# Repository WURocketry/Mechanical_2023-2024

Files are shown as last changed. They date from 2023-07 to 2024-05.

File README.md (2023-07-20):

# Mechanical
Mechanical Design Repository

* CAD Models

### Subteam Folders
Subteams are free to modify their own folder as they like - keep all your subteam related files/articles/figures within that folder.

### Subteam Branches
The "main" Mechanical repository is organized into 5 subteam development branches:

* "dev/aero"
* "dev/avionics"
* "dev/payload"
* "dev/r&p"
* "dev/structures"

Subteam changes should be pushed and pull requests made only to the respective development subteam branch!

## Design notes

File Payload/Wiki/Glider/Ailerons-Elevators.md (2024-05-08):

### How do planes turn with their ailerons?
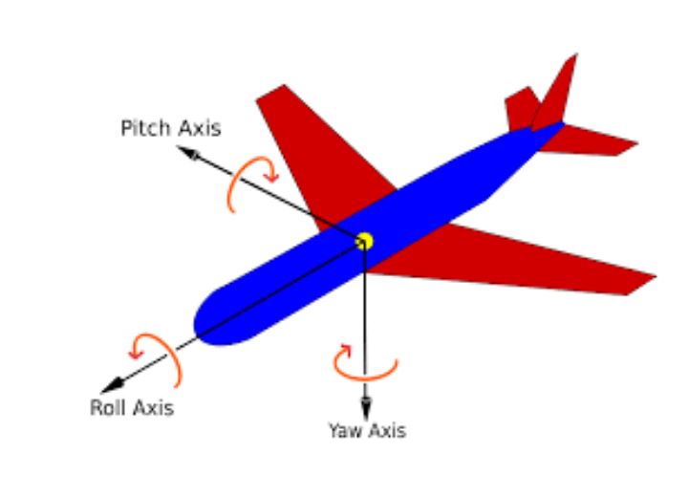
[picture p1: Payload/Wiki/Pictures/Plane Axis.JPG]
Plane Axis


An aircraft is turned by banking the wing. This is achieved via aileron deflection (the flaps on the wings). For example, if wanting to turn left, the left aileron would go up and the right aileron would go down. The right wing would generate comparatively more lift and cause the aircraft to rotate along the roll axis toward the left wing. Breaking down the lift into its constituent vectors, it can be seen the aircraft will turn left. However, in generating lift by deflecting the airflow, more drag is necessarily incurred on the right wing. This causes the aircraft to rotate along the yaw axis toward the right wing. This is known as adverse yaw. A rudder can be used to counteract this skidding effect by turning it opposite the direction of the slip. 

Aside: To compensate for the decrease in lift due to ailerons, consider the use of an elevator to maintain altitude

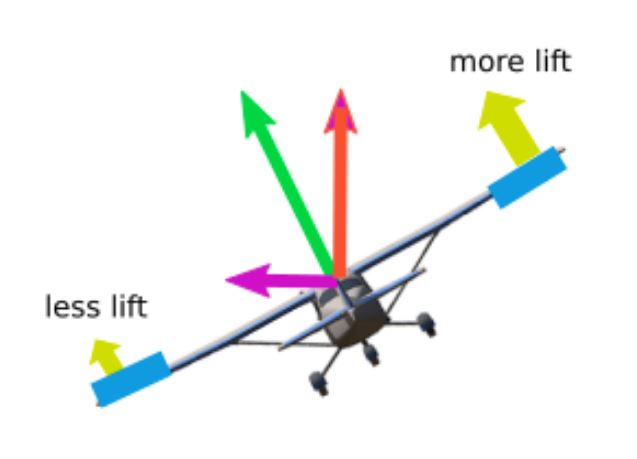
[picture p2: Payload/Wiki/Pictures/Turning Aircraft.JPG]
Turning Aircraft


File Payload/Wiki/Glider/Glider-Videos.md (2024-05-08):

## These are all videos that I've watched when trying to learn about gliders and planes

[Can a plane fly with offset wings?](https://youtu.be/_6qv-7W1oXM?si=U3Id_NZv6tD9XoEl)

[Air powered plane](https://youtu.be/Ho2l1K4Jprg?si=fbuXTHSk7X7ttCQ5)

[In-air deployed Wings](https://youtu.be/bcsHTJZXA5M?si=50AS-EBUmxvygqyN)

[Building RC Planes with a 3D printer](https://youtu.be/Fi35p8bJMsA?si=6PIT_olx3aTciqMt)

[Lifting body Aircraft](https://youtu.be/PmRX-CzJbd0?si=Z4fhiQjwDQRD28tA)

[Shuttle Drop Glider](https://youtu.be/U6PQD6Xdg0g?si=6WSX85FjxjvWDiC7)

[Solid Wood Glider](https://youtu.be/7oy3jXu_DmY?si=__zFUrIsEFcsmnhw)

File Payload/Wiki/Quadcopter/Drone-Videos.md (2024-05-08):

## These are all videos that I've watched when trying to learn about drones and quadcopters

[Building the world's fastest drone](https://youtu.be/szxRORFl_lc?si=UBYPmssPb1zO7FjE)

[Ground Effect Quadcopter](https://youtu.be/66PmaluCvbU?si=f91-r_Z-RgY1vGZZ)

[Vertical Drone with Flaps](https://youtu.be/AnGWM0yDfpo?si=fNXaneckABWPh2j7)

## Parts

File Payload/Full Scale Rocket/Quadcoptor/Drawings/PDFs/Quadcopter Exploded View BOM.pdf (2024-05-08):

ITEM NO. | PART NUMBER | DESCRIPTION | QTY.
1 | Vertical Beam | | 1
2 | Arm Hub | | 1
3 | ECO II Series 2207 | | 4
4 | Left Hinge | | 4
5 | Right Hinge | | 4
6 | Arm | | 4
7 | DAL Fold 2 | | 4
8 | Turnigy 6S 5000 mAh Battery | | 1
9 | Speedy Bee F405 V3 Stacked FC & ESC | | 1
10 | Nosecone | | 1
11 | 1556A24 | Zinc-Plated Steel Corner Bracket | 8
12 | 91772A092 | Passivated 18-8 Stainless Steel Pan Head Phillips Screw | 12
13 | Life Support Electronics Board | | 1
14 | Detachment Eye Nut | | 1
15 | Arm Cushion | | 4
16 | STEMnaut Housing | | 1
17 | Arm Locker | | 4
18 | Hinge Cushion | | 4
19 | 91773A151 | Stainless Steel Decorative Round Head Phillips Screws | 6
20 | 90272A161 | Zinc-Plated Steel Pan Head Phillips Screw | 2
21 | STEMnaut Housing Cap | | 1
22 | 91292A134 | 18-8 Stainless Steel Socket Head Screw | 4
23 | Leadscrew Motor | | 1
24 | Motor Shaft Coupler | | 1
25 | Leadscrew | | 1
SOLIDWORKS Educational Product. For Instructional Use Only.

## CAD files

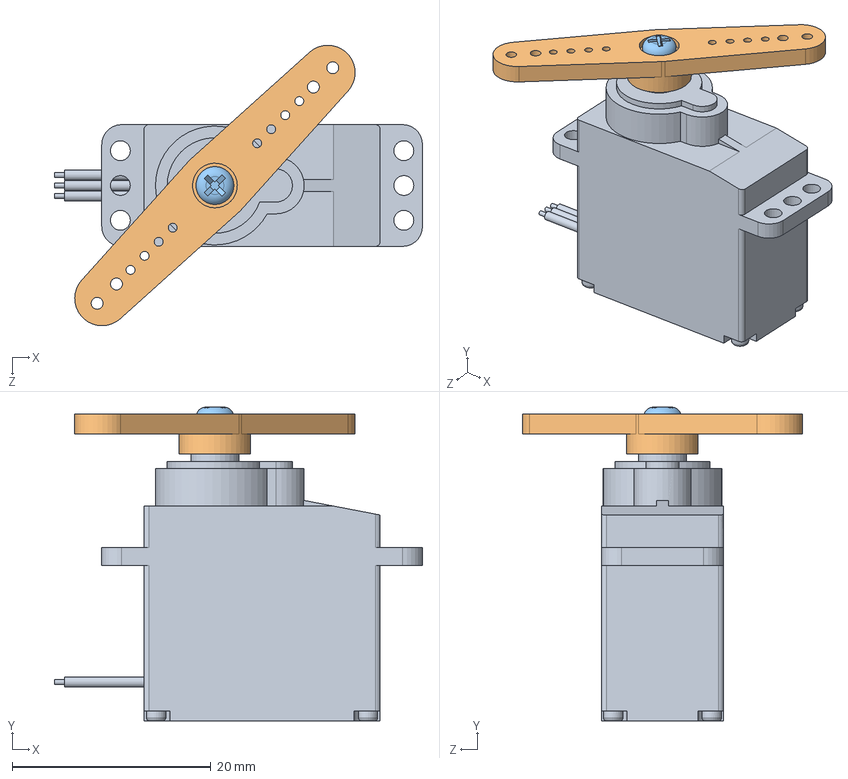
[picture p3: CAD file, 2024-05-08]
Payload/Full Scale Rocket/Quadcoptor/arduino-micro-servo-1.snapshot.13/SM-S2309S.SLDASM
37.0 x 31.5 x 28.2 mm
SM-S2309S
SM-S2309S-Arm
SM-S2309S-Screw

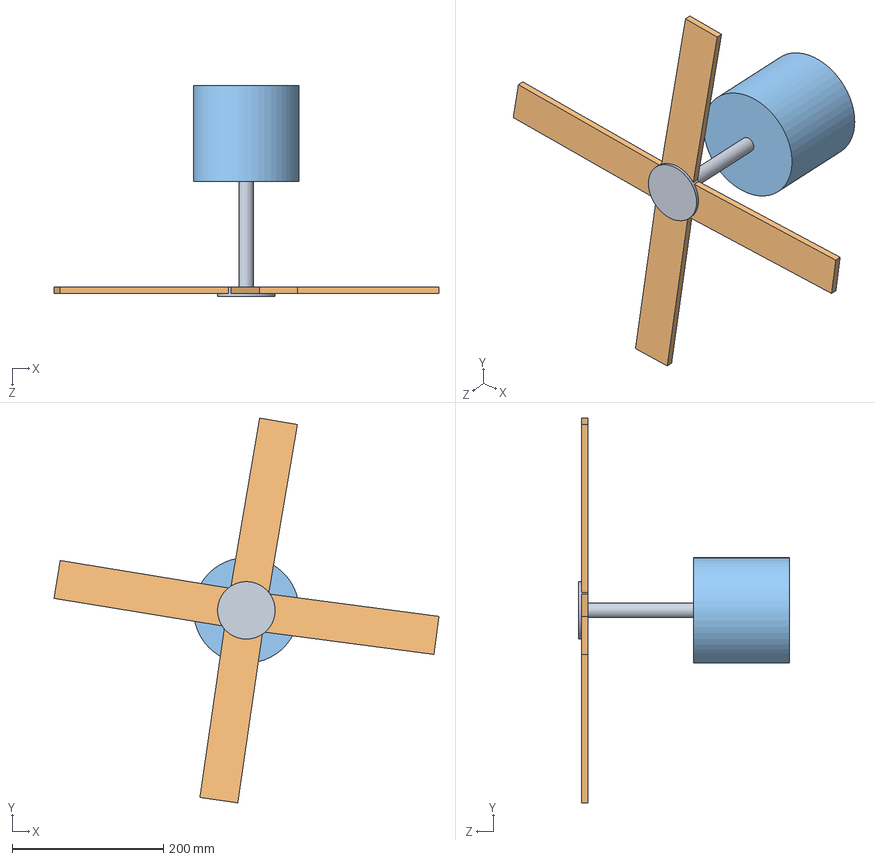
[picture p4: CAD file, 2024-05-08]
Payload/Autorotation Prelim/Autorotation_ASS.SLDASM
509.9 x 509.7 x 279.4 mm
Rotor Shaft
Rotor Blades x 4
Capsule

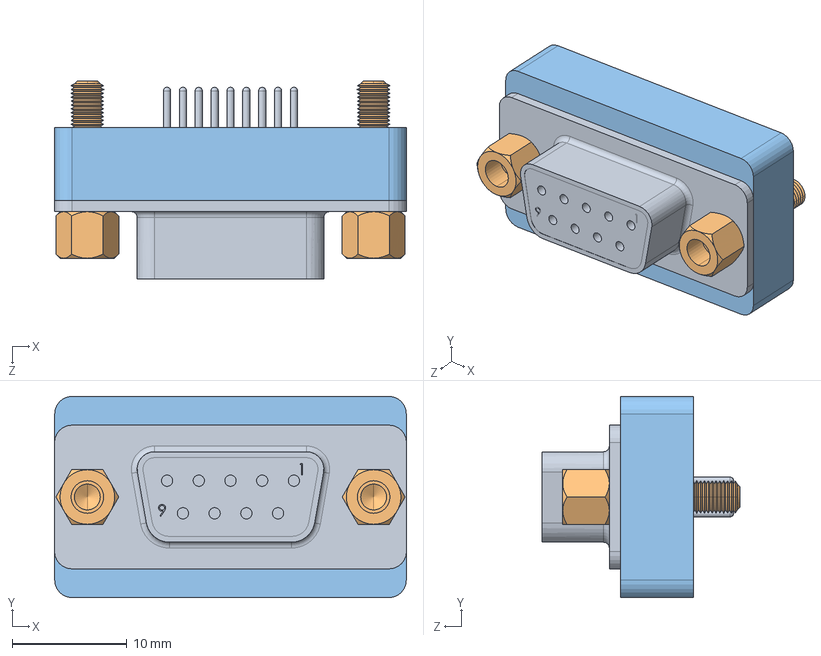
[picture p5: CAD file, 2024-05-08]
Payload/Full Scale Rocket/Aft Assembly/Airbrakes/Connector/ConnectorAssembly.SLDASM
30.7 x 17.6 x 17.3 mm
FS_DB9_Female_Port
FS_DB9_Screw x 2
Part1^ConnectorAssembly

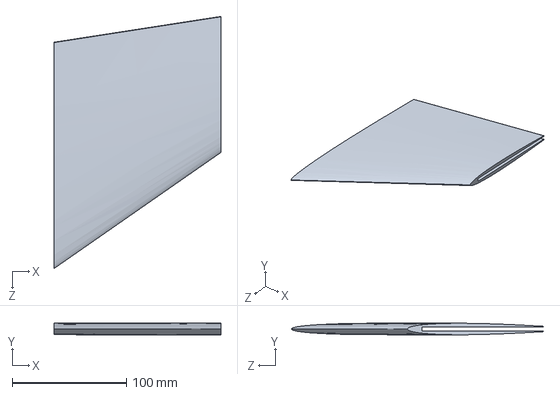
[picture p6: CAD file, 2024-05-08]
Structures/Aerodynamic Test Article/Fin Research/fullscale_fincover3.3 (1).SLDPRT
146.1 x 10.2 x 220.5 mm

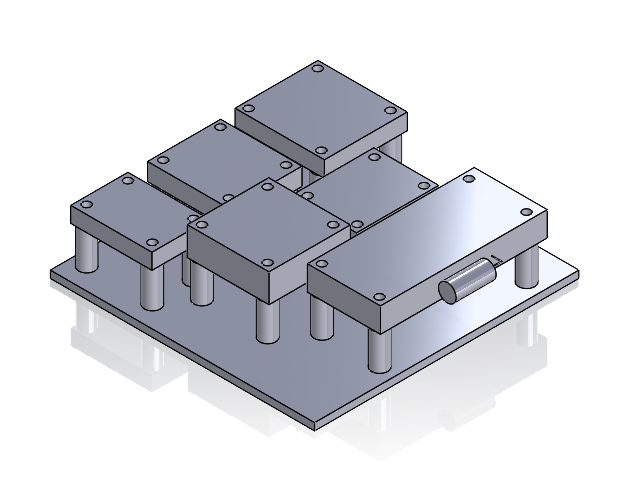
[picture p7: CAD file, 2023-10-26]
Payload/Electronics Board/EBoard_NEW.SLDASM
Base_NEW
RP2-B2_NEW
BME680_NEW
QWIIC OpenLog_NEW
BN008x 900F_NEW
MAX 17048_NEW
GPS_NEW
CoiledAntenna_NEW

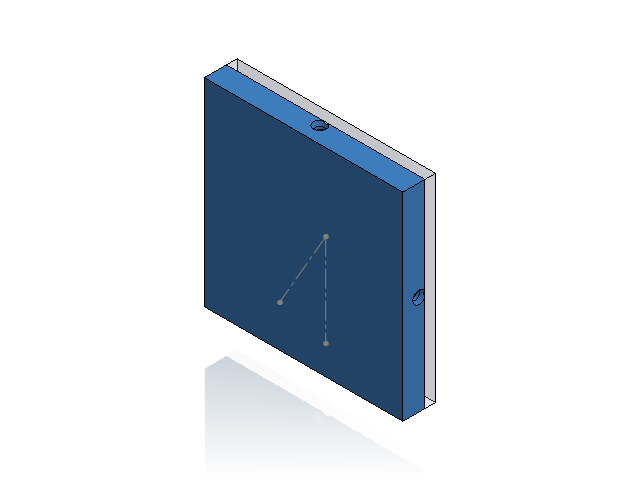
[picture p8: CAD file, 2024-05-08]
Payload/Full Scale Rocket/Manufacturing Jigs/Aft_Bulkhead_Jig_Visualization.SLDASM
FS_Aft_Bulkhead_Jig_p1
FS_Aft_Bulkhead_Jig_p2
FS_Airbrakes_Section_Coupler

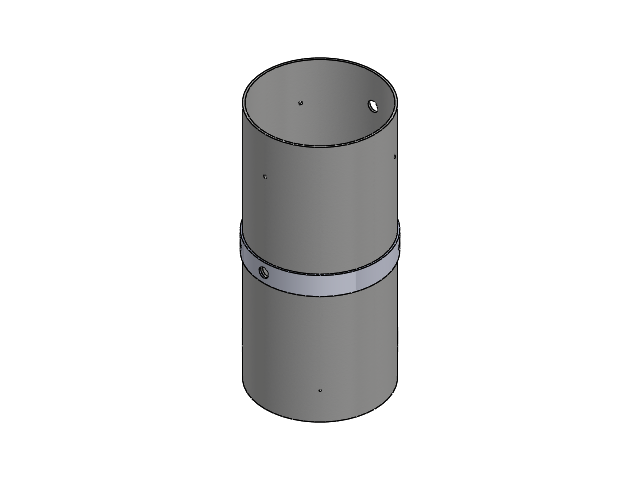
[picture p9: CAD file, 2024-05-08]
Payload/Full Scale Rocket/Mid And Coupler/Mid_and_Coupler.SLDASM
FS_Avionics_Coupler
FS_Mid_Body_Tube

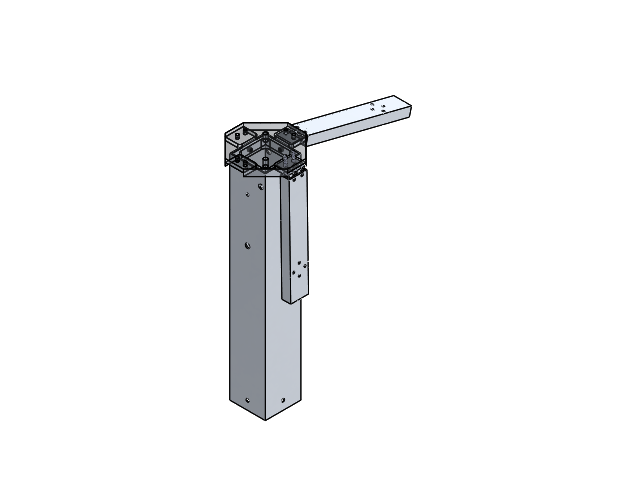
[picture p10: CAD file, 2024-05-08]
Payload/Full Scale Rocket/Quadcoptor/Hinges/HingeDemo.SLDASM
Hinge_Leaf x 4
Hinge_Pin x 2
Quadcopter_Arm_Hub
Quadcopter_Arm x 2
Quadcopter_Vertical_Beam
91773A151_Stainless Steel Decorative Round Head Phillips Screws x 2

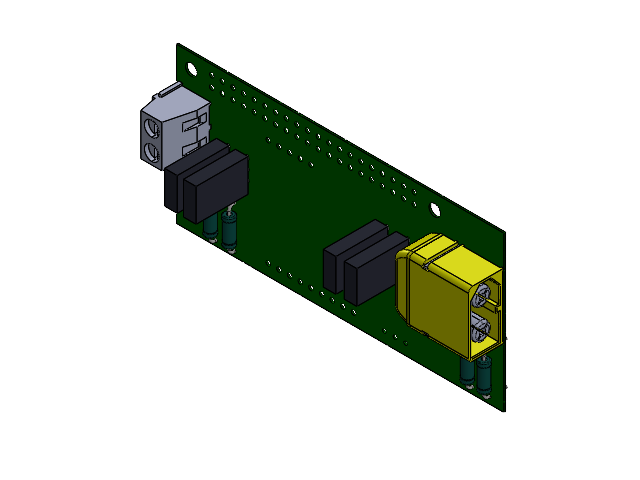
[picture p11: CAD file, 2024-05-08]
Payload/Full Scale Rocket/Quadcoptor/Sled/RPi-Zero-HAT (65 x 30 mm).SLDASM
6328297200_1.step
1_1.step x 4
2_1.step x 4
Vishay_1.step x 4
Extruded_1.step x 4
Extruded-0_1.step x 12
Extruded-1_1.step x 12
c-282836-2-h-3d_1.step

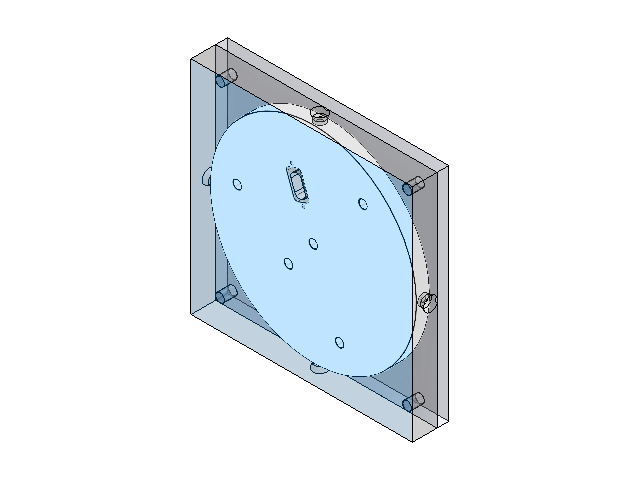
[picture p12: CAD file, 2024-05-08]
Structures/Full Scale/Manufacturing Jigs/Aft_Bulkhead_Jig_Visualization.SLDASM
FS_Aft_Bulkhead_Jig_p1
FS_Aft_Bulkhead_Jig_p2
FS_Airbrakes_Section_Coupler

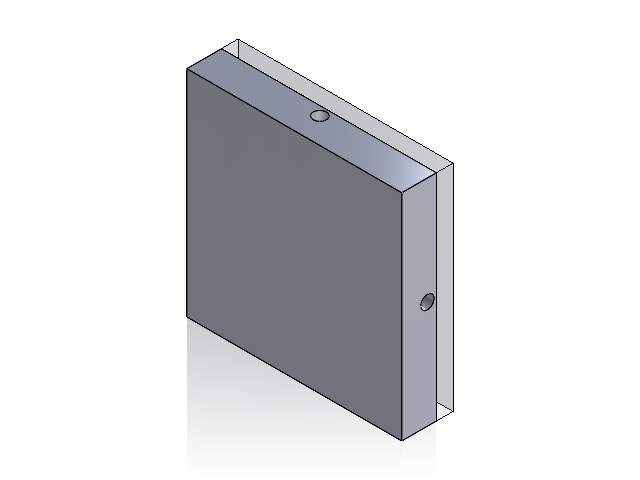
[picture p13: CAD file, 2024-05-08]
Structures/Sub Scale/Manufacturing Jigs/Aft Bulkhead Jig Visualization.SLDASM
SS_Aft_Bulkhead_Jig_p1
SS_Airbrakes_Bulkhead
SS_Aft_Bulkhead_Jig_p2

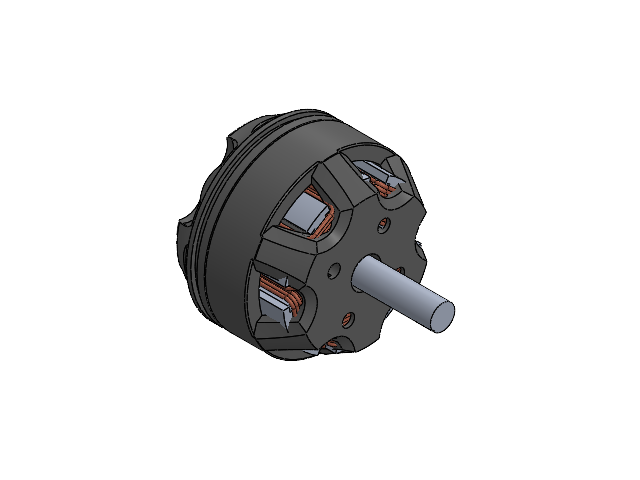
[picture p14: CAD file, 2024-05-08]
Payload/Full Scale Rocket/Quadcoptor/Motors/Motor_Body.SLDASM
Stator
Interior
Axle
radial ball bearing_68_skf x 2
Bell

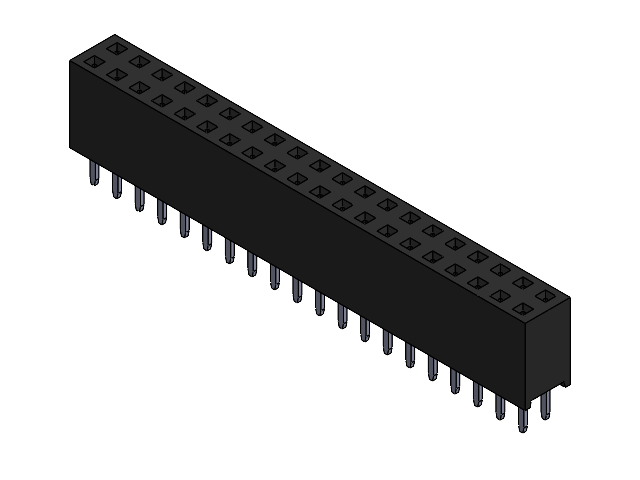
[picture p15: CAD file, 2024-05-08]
Payload/Full Scale Rocket/Quadcoptor/Sled/PPTC202LFBN-RC.SLDASM
2 row tin body_20.step
2 row tin pins.step x 20

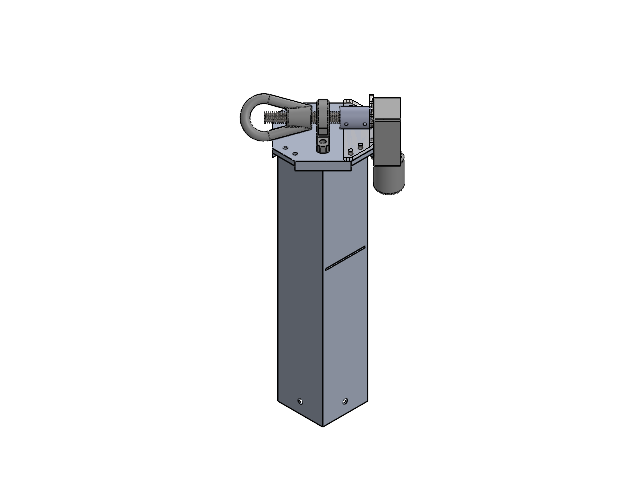
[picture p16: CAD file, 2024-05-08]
Payload/Full Scale Rocket/Quadcoptor/Subassemblies/Detachment Subassembly.SLDASM
Quadcopter_Vertical_Beam
Quadcopter_Arm_Hub
91772A092_Passivated 18-8 Stainless Steel Pan Head Phillips Screw x 4
Leadscrew Motor
Motor Shaft Coupler
Leadscrew
Motor Mount
3274T41_Steel Oval Eye Nut- for Lifting
4491N16_Low-Profile Mounted Ball Bearing

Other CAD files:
Payload/Full Scale Rocket/Aft Assembly/Airbrakes/Harness_1-FS_Airbrake_Assembly.SLDASM
Payload/Full Scale Rocket/Quadcoptor/Sled/PCE/PCE_HAT_v1-0.step.SLDASM
Structures/Full Scale/Fwd Assembly/FS_Fwd_Assembly.SLDASM
Payload/Autorotation Prelim/Capsule.SLDPRT
Payload/Autorotation Prelim/Rotor Blades.SLDPRT
Payload/Autorotation Prelim/Rotor Shaft.SLDPRT
Payload/Electronics Board/BME680_NEW.SLDPRT
Payload/Electronics Board/BN008x 900F_NEW.SLDPRT
Payload/Electronics Board/Base_NEW.SLDPRT
Payload/Electronics Board/EBoard_NEW.SLDPRT
Payload/Electronics Board/GPS_NEW.SLDPRT
Payload/Electronics Board/MAX 17048_NEW.SLDPRT
Payload/Electronics Board/QWIIC OpenLog_NEW.SLDPRT
Payload/Electronics Board/RP2-B2_NEW.SLDPRT
Payload/Full Scale Rocket/Aft Assembly/Airbrakes/7811K128_Multipurpose 660 Leaded Sleeve Bearing.SLDPRT
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

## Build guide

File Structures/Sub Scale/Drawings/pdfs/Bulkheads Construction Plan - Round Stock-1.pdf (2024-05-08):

Key: | Equipment | Tools

## Fullscale

All Bulkheads
- Set up the round vice (indexer?) on the vertical mill
- Face the part down to the required thickness
- Note: These steps will likely be easier to program than to do manually
- Use a dial caliper to measure the stock thickness and diameter and record both
- Secure the stock in the vice
- Edgefind (at ~1200 rpm), then set the center of the part at (0,0)
- Use a ½” 2-flute endmill to touch off the top of the part and lock the quill.
- Move the bed out of the way of the endmill
- Using the number you recorded for the stock thickness, move the knee up the appropriate amount to face the part
■ The 2 Avionics Bulkheads need to be 0.25” thick and the Forward and Aft Bulkheads need to be 0.375” thick
■ Example: If you measure the stock to be 0.500” thick and are making an Avionics Bulkhead, you must move the knee up (0.5-0.25=)0.250”
- At an rpm of | , face the part, taking off ~0.020 per pass

200*4
0.5 = 1600 rpm
- Before altering your setup, double-check the thickness of your bulkhead Note: from this point, the bulkhead designs will diverge. Be sure to follow the relevant procedures.

Forward Bulkhead
- Use one of the 0.375” thick pieces
- Use a center drill to mark holes
| ○ At (0,0)
- At 1” above (forward of from where you are standing) the part’s center
- Eye Bolt
- Use a 6.6mm drill bit to drill a hole in the center of the part (at (0,0)) at an rpm of
| 200*4 0.259843 = 3075 rpm ■ M6 eye bolt
- Manufacturing jig hole
- Use a ⅛” drill bit to drill a hole 1” above the center of the part at an rpm of
| 200*4 0.125 = 6400 rpm
- Remove the part from the vise and place it into the Forward Bulkhead Manufacturing Jig such that the bulkhead aligns with the jig’s pegs
- Either remove the round vice or move to another machine with a standard vice
- Place the manufacturing jig/bulkhead into the vice perpendicular such that the 6”x6” face of the part is facing you (at the front of the machine)
- Use a mechanical stop when securing the part in the vice to increase
| manufacturing speed

- M4 Holes
- Edgefind (at~1200 rpm), set the center of the part at (0,0)
■ This should align with the perpendicular holes in the jig
- Use a center drill to mark a hole at (0,0)
■ The jig may be too thick for this. If it is, ignore this step
- Place a 3.3mm drill bit into the mill
- Set the plunge depth to 0.5”
■ With the mill not running, touch the drill to the part
■ Lock the quill
■ Set the quill stop
■ Raise the quill
■ Raise the knee 0.5”
- Drill the hole at an rpm of

200*4
0.118 = 6770 rpm
- Rotate the part 90 degrees clockwise (or counter-clockwise so long as you’re consistent) and repeat these steps until all four sides of the part have a hole at its center
- Use an M4x0.70 tap (in the vertical mill to decrease likelihood of breaking a tap) to tap the hole
- Rotate the part 90 degrees clockwise (or counter-clockwise so long as you’re consistent) and repeat this step until all four sides of the part have a threaded M4x0.70 hole at its center
- Remove the part from the mill and inspect it. Ensure that the applicable above steps have been followed
- Use dial calipers to check the diameter of your bulkhead
- If necessary, turn the part down to a 6” diameter circle on the lathe
- Turn the jaws of the lathe such that the pieces of the jaws that protrude furthest in the machine’s Z direction are toward the spindle’s axis of rotation
- Use a live center to FIRMLY press the part against the jaws
■ The live center should be pressing into the eye bolt hole on the forward and aft bulkheads
■ Place a shop towel between the part and the jaws
- With the machine off, LIGHTLY touch the turning tool to the edges of the part. Set this as your measured diameter in the X direction.
- Back the cutting tool away (in the X and Z directions) such that the rotation of the part clears the cutting tool in both the X and Z directions.
- GRADUALLY turn the part down to 3” radius by making passes at it with the
turning tool at an rpm of | (preferably considerably less)

200*4
6 = 133 rpm

Aft Bulkhead
- Use one of the 0.375” thick pieces
- Use a center drill to 7 mark holes according to dimensional drawing
- Because the holes are defined according to angles and radii, program the holes for use with the center drill and drill bits later

- 1x at (0,0) (for center bushing)
- 1x for eye bolt hole
- 3x for airbrake paddle screws
- 2x for wiring hole Connector
- Center Bushing bolt hole
- Use a 6.6mm drill bit to drill a hole in the center of the part (at (0,0)) at an rpm of

200*4
0.259843 = 3075 rpm
■ Note: 6.6mm=0.259843”
■ M6 bolt
- Eye bolt hole
- Use a 6.6mm drill bit to drill a hole at an rpm of

200*4
0.259843 = 3075 rpm
■ Note: 6.6mm=0.259843”
■ M6 Eye bolt
- Airbrake paddle holes
- Metric: Use a 6.6mm drill bit to drill 3 holes (or use the bolt hole pattern) at an rpm of

200*4
0.259843 = 3075 rpm
■ M6 screws
- Wire connector holes
- Use a #43 drill bit to drill the holes at an rpm of

200*4
0.089 = 8900 rpm
- Before moving on, go ahead and use a #4-40 tap (in the mill for stability… BE CAREFUL!) so that you don’t have to find the hole again
- Wire Connector Hole
- Use a ⅛” end mill and program a rectangular pocket through the part according to the dimensional drawing
■

200*4
0.125 = 6400 rpm
■ Note: The dimensions in the drawing are for programming the pocket
- BEFORE REMOVING THE BULKHEAD FROM THE VISE use a sharpie to mark a vertical line at the right of the part. This line should be on the right side of an airbrake paddle hole
- Remove the part from the vise and place it into the Aft Bulkhead Manufacturing Jig such that the bulkhead aligns with the jig’s pegs
- The line you drew should line up with a slot on the inside of the manufacturing jig. This ensures that the bulkhead is oriented correctly. Both the slot and the line should be facing you.
- Either remove the round vice or move to another machine with a standard vice
- Place the manufacturing jig/bulkhead into the vice perpendicular such that the 6”x6” face of the part is facing you (at the front of the machine)
- Use a mechanical stop when securing the part in the vice to increase manufacturing speed
- M4 Holes
- Edgefind (at~1200 rpm), set the center of the part at (0,0)
■ This should align with the perpendicular holes in the jig

- Use a center drill to mark a hole at (0,0)
■ The jig may be too thick for this. If it is, ignore this step
- Place a 3.3mm drill bit into the mill
- Set the plunge depth to 0.5”
■ With the mill not running, touch the drill to the part
■ Lock the quill
■ Set the quill stop
■ Raise the quill
■ Raise the knee 0.5”
- Drill the hole at an rpm of

200*4
0.118 = 6770 rpm
- Rotate the part 90 degrees clockwise (or counter-clockwise so long as you’re consistent) and repeat these steps until all four sides of the part have a hole at its center
- Use an M4x0.70 tap (in the vertical mill to decrease likelihood of breaking a tap) to tap the hole
- Rotate the part 90 degrees clockwise (or counter-clockwise so long as you’re consistent) and repeat this step until all four sides of the part have a threaded M4x0.70 hole at its center
- Inspect the part to ensure that the applicable above steps have been followed. Remove the part from the mill.
- Use dial calipers to check the diameter of your bulkhead and test its fit
- If necessary, turn the part down to a 6” diameter circle on the lathe
- Turn the jaws of the lathe such that the pieces of the jaws that protrude furthest in the machine’s Z direction are toward the spindle’s axis of rotation
- Use a live center to FIRMLY press the part against the jaws
■ The live center should be pressing into the eye bolt hole on the forward and aft bulkheads
■ Place a shop towel between the part and the jaws
- With the machine off, LIGHTLY touch the turning tool to the edges of the part. Set this as your measured diameter in the X direction.
- Back the cutting tool away (in the X and Z directions) such that the rotation of the part clears the cutting tool in both the X and Z directions.
- GRADUALLY turn the part down to 3” radius by making passes at it with the
turning tool at an rpm of | (preferably considerably less)

200*4
6 = 133 rpm

Forward and Aft AVIONICS Bulkheads
- Use one of the 0.25” round stock pieces
- Secure “round vise” in standard vise and secure material stock in round vise
- Slot pattern for Avionics board
- Make a 2 plunge cuts using a 0.25” 2-flute endmill (might be easier to program)
- Center Drill various holes according to dimensional drawing
- 2x M10 Lead screw holes
- 2x Black Powder Cup mounting holes

- 1x Wire hole
■ AFT ONLY
- 2x Wire Connector Holes
- MUST center drill for a “hole” at (0,0) for lathe operations later
- Make Holes
- 2x M10 Lead Screw Holes (medium fit)
■ Use an 11mm drill bit at an rpm of | (or less)

200*4
0.433071 = 1847 rpm
- Note: Cutting speed for aluminum is 200 SFPM; 11mm=0.433071”
- 2x Black Powder Cup mounting holes
■ Use a #36 (0.107”) drill bit at an rpm of | (or less)

400*4
0.107 = 14950 rpm
- Wire hole(s)
■ Use a 3/16” (0.1875”) drill bit at an rpm of | (or less)

200*4
0.1875 = 7470 rpm
- AFT ONLY
- Wire Connector Hole
■ Use a ⅛” end mill and program a rectangular pocket through the part according to the dimensional drawing
●

200*4
0.125 = 6400 rpm
- Note: The dimensions in the drawing are for programming the pocket
- Ensure that the above steps have been followed before removing the part from the vise!
- If necessary, turn the part down to a 6” diameter circle on the lathe
- Measure and record the current bulkhead diameter
- Turn the jaws of the lathe such that the pieces of the jaws that protrude furthest in the machine’s Z direction are toward the spindle’s axis of rotation
- Use a live center to FIRMLY press the part against the jaws
■ The live center should be pressing into the center drilled “hole” on the forward and aft avionics bulkheads
■ Place a shop towel between the part and the jaws
- With the machine on, LIGHTLY touch the turning tool to the edge of the part. Set the X direction value to the value you recorded for the part’s current diameter.
- GRADUALLY turn the part down to a 3” radius
■

200*4
6 = 133 rpm
- Use the lathe and turning tool to turn a ⅛” (Z direction) lip into the part such that the smaller section diameter of the part is 5.83” in diameter (2.915” in radius). This smaller diameter should be located on the same side as the avionics board slots
ALL BULKHEADS
- Check that the part slides into the body tube. Gradually turn off more material with the lathe and turning tool until you are subjectively satisfied with the fit of the part
- Clean up your work area or face the consequences

Key: | Equipment | Tools

## Subscale

All Bulkheads
- Set up the round vice (indexer?) on the vertical mill
- Edgefind (at ~1200 rpm) on the bulkhead and center drill a divot in the center
- Or continue to drill a hole of the required size for the forward and aft bulkheads
- Flip the bulkhead around and do the same to the other side
- It’s pretty important that the holes
- Flip the jaws around on the lathe
- Face the part down to the required thickness
- Use a dial caliper to measure the stock thickness and diameter and record both
- Use the live center to press the stock against the chuck FIRMLY
■ Use a shop towel between the work and the chuck
- Using the number you recorded for the stock thickness, face the part down to the
| required thickness
■ The 2 Avionics Bulkheads need to be 0.25” thick and the Forward and Aft Bulkheads need to be 0.375” thick
- At an rpm of | or LESS, face the part, taking off ~0.010 per pass

200*4
4 = 200 rpm
down to a ~½” circle around the live center
- Avionics Bulkheads:
- Before moving on, turn the lip
- If this gives you trouble, then you can do the step with a circular profile on the
| lathe later
- Turn the part down to its required diameter about ⅔ of the way down the part, then flip it over and do the same to the last third
- Check the bulkhead’s fit into the body tube before moving on and make adjustments as
| necessary
- Move to the vertical mill and the round vise. Edgefind and set the center of the part to be (0,0)
Note: from this point, the bulkhead designs will diverge. Be sure to follow the relevant procedures.

Forward Bulkhead
- Use one of the 0.375” thick pieces
- Face off the circle that was used on the lathe with the live center
- Use a center drill to mark holes
| ○ At (0,0)
- At 1” above (forward of from where you are standing) the part’s center
- Eye Bolt
- Use a 6.6mm drill bit to drill a hole in the center of the part (at (0,0)) at an rpm of
| 200*4 0.259843 = 3075 rpm ■ M6 eye bolt

- Manufacturing jig hole
- Use a ⅛” drill bit to drill a hole 1” above the center of the part at an rpm of

200*4
0.125 = 6400 rpm
- Remove the part from the vise and place it into the Forward Bulkhead Manufacturing Jig such that the bulkhead aligns with the jig’s pegs
- Either remove the round vice or move to another machine with a standard vice
- Place the manufacturing jig/bulkhead into the vice perpendicular such that the 4” diameter face of the part is facing you (at the front of the machine)
- Use a mechanical stop when securing the part in the vice to increase manufacturing speed
- M4 Holes
- Edgefind (at~1200 rpm), set the center of the part at (0,0)
■ This should align with the perpendicular holes in the jig
- Use a center drill to mark a hole at (0,0)
■ The jig may be too thick for this. If it is, ignore this step
- Place a 3.3mm drill bit into the mill
- Set the plunge depth to 0.5”
■ With the mill not running, touch the drill to the part
■ Lock the quill
■ Set the quill stop
■ Raise the quill
■ Raise the knee 0.5”
- Drill the hole at an rpm of

200*4
0.118 = 6770 rpm
- Rotate the part 90 degrees clockwise (or counter-clockwise so long as you’re consistent) and repeat these steps until all four sides of the part have a hole at its center
- Use an M4x0.70 tap (in the vertical mill to decrease likelihood of breaking a tap) to tap the hole
- Rotate the part 90 degrees clockwise (or counter-clockwise so long as you’re consistent) and repeat this step until all four sides of the part have a threaded M4x0.70 hole at its center
- Remove the part from the mill and inspect it. Ensure that the applicable above steps have been followed
- Use dial calipers to check the dimensions of your bulkhead

Aft Bulkhead
- Use one of the 0.375” thick pieces
- Face off the circle that was used on the lathe with the live center
- Use a center drill to 7 mark holes according to dimensional drawing
- Because the holes are defined according to angles and radii, program the holes for use with the center drill and drill bits later
- 1x at (0,0) (for center bushing)
- 1x for eye bolt hole

- 3x for airbrake paddle screws
- 2x for wiring hole Connector
- Center Bushing bolt hole
- Use a 6.6mm drill bit to drill a hole in the center of the part (at (0,0)) at an rpm of

200*4
0.259843 = 3075 rpm
■ Note: 6.6mm=0.259843”
■ M6 bolt
- Eye bolt hole
- Use a 6.6mm drill bit to drill a hole at an rpm of

200*4
0.259843 = 3075 rpm
■ Note: 6.6mm=0.259843”
■ M6 Eye bolt
- Airbrake paddle holes
- Metric: Use a 6.6mm drill bit to drill 3 holes (or use the bolt hole pattern) at an rpm of

200*4
0.259843 = 3075 rpm
■ M6 screws
- Wire connector holes
- Use a #43 drill bit to drill the holes at an rpm of

200*4
0.089 = 8900 rpm
- Before moving on, go ahead and use a #4-40 tap (in the mill for stability… BE CAREFUL!) so that you don’t have to find the hole again
- Wire Connector Hole
- Use a ⅛” end mill and program a rectangular pocket through the part according to the dimensional drawing
■

200*4
0.125 = 6400 rpm
■ Note: The dimensions in the drawing are for programming the pocket
- BEFORE REMOVING THE BULKHEAD FROM THE VISE use a sharpie to mark a vertical line at the right of the part. This line should be on the right side of an airbrake paddle hole
- Remove the part from the vise and place it into the Aft Bulkhead Manufacturing Jig such that the bulkhead aligns with the jig’s pegs
- The line you drew should line up with a slot on the inside of the manufacturing jig. This ensures that the bulkhead is oriented correctly. Both the slot and the line should be facing you.
- Either remove the round vice or move to another machine with a standard vice
- Place the manufacturing jig/bulkhead into the vice perpendicular such that the 4” diameter face of the part is facing you (at the front of the machine)
- Use a mechanical stop when securing the part in the vice to increase manufacturing speed
- M4 Holes
- Edgefind (at~1200 rpm), set the center of the part at (0,0)
■ This should align with the perpendicular holes in the jig
- Use a center drill to mark a hole at (0,0)
■ The jig may be too thick for this. If it is, ignore this step

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

200*4
0.118 = 6770 rpm
- Rotate the part 90 degrees clockwise (or counter-clockwise so long as you’re consistent) and repeat these steps until all four sides of the part have a hole at its center
- Use an M4x0.70 tap (in the vertical mill to decrease likelihood of breaking a tap) to tap the hole
- Rotate the part 90 degrees clockwise (or counter-clockwise so long as you’re consistent) and repeat this step until all four sides of the part have a threaded M4x0.70 hole at its center
- Inspect the part to ensure that the applicable above steps have been followed. Remove the part from the mill.

Forward and Aft AVIONICS Bulkheads
- Use one of the 0.25” round stock pieces
- Face off the circle that was used on the lathe with the live center
- Secure “round vise” in standard vise and secure material stock in round vise
- Slot pattern for Avionics board
- Make a 2 plunge cuts using a 0.25” 2-flute endmill (might be easier to program)
- Center Drill various holes according to dimensional drawing
- 2x M10 Lead screw holes
- 2x Black Powder Cup mounting holes
- 1x Wire hole
■ AFT ONLY
- 2x Wire Connector Holes
- Make Holes
- 2x M10 Lead Screw Holes (medium fit)
■ Use an 11mm drill bit at an rpm of | (or less)

200*4
0.433071 = 1847 rpm
- Note: Cutting speed for aluminum is 200 SFPM; 11mm=0.433071”
- 2x Black Powder Cup mounting holes
■ Use a #36 (0.107”) drill bit at an rpm of | (or less)

200*4
0.107 = 7470 rpm
- Wire hole(s)
■ Use a 3/16” (0.1875”) drill bit at an rpm of | (or less)

200*4
| 0.1875 = 7470 rpm
- AFT ONLY
- Wire Connector Hole

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

200*4
0.125 = 6400 rpm
- Note: The dimensions in the drawing are for programming the pocket
- Ensure that the above steps have been followed before removing the part from the vise! ALL BULKHEADS
- Check that the part slides into the body tube. Gradually turn off more material with the lathe and turning tool until you are subjectively satisfied with the fit of the part
- Clean up your work area or face the consequences

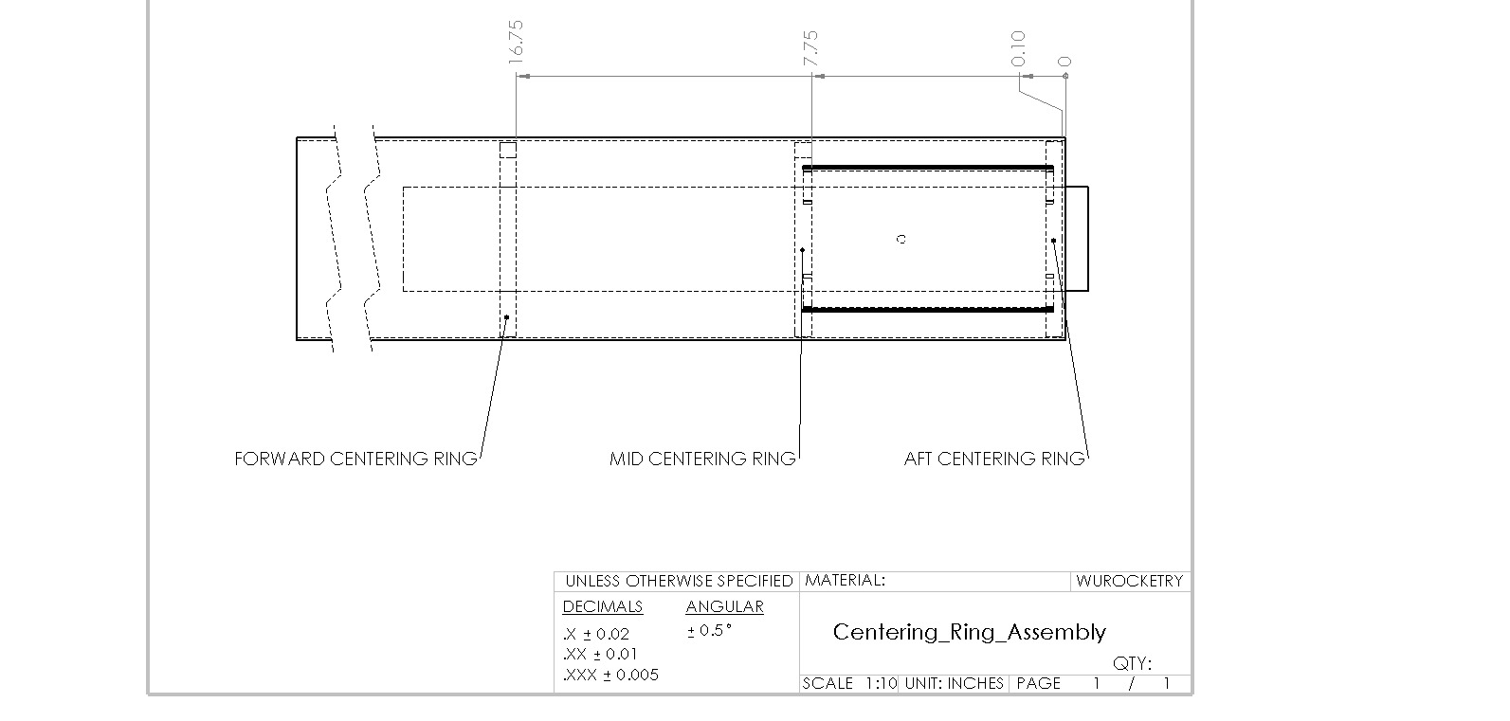
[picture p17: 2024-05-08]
Structures/Full Scale/Drawings/Images/Centering_Ring_Assembly.JPG

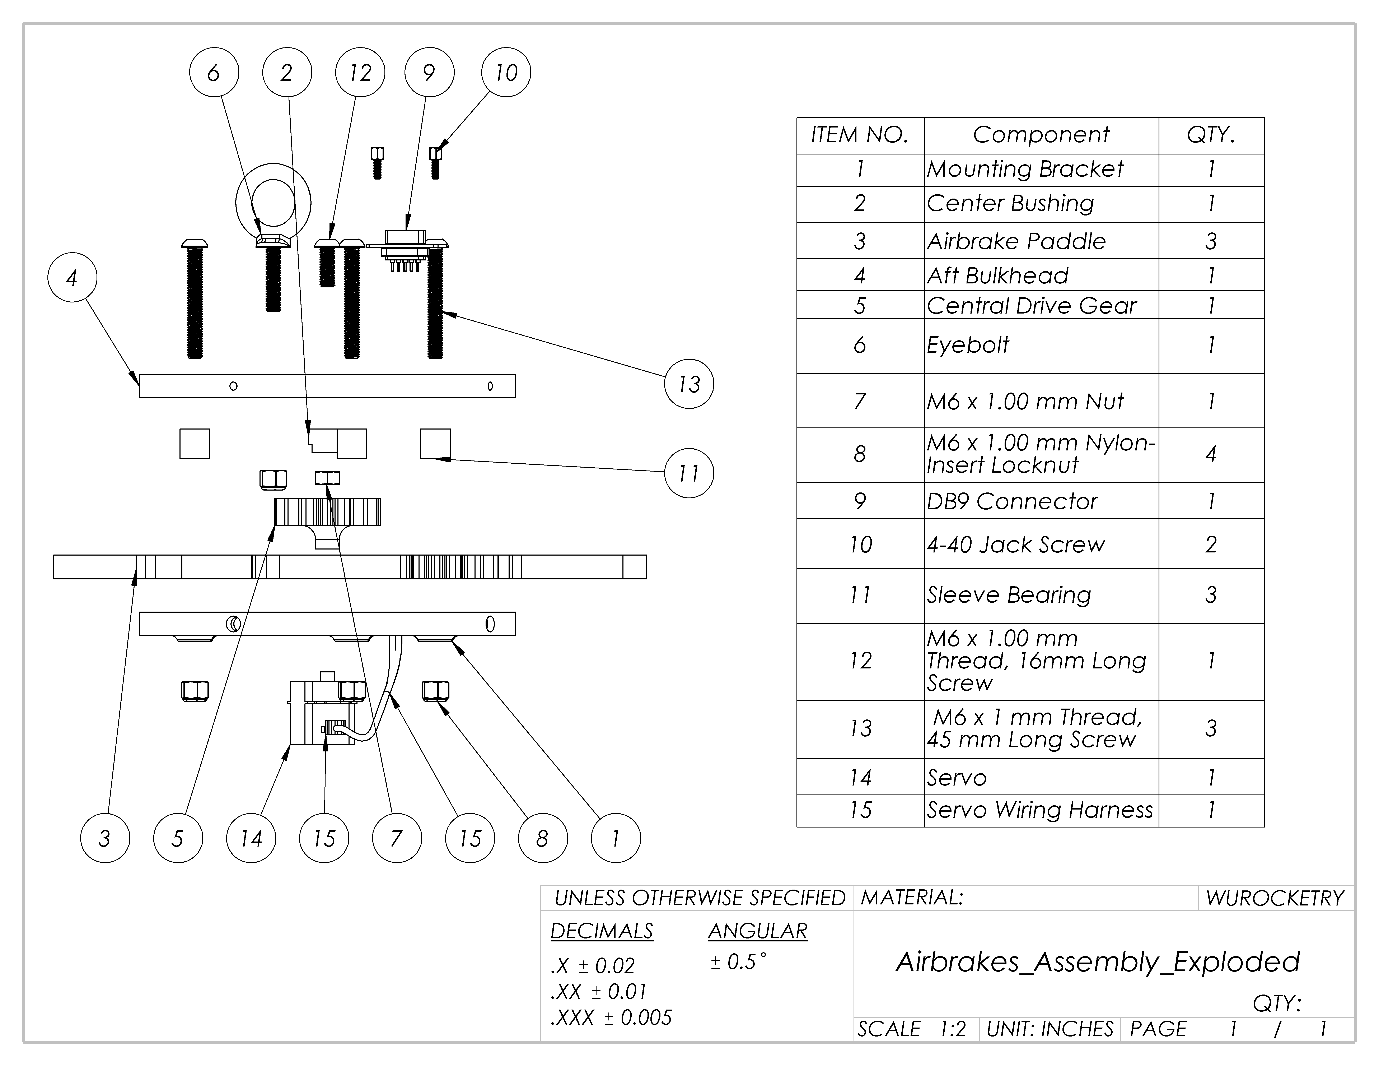
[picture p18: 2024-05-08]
Payload/Full Scale Rocket/Drawings/Images/Airbrakes_Assembly_Exploded.PNG

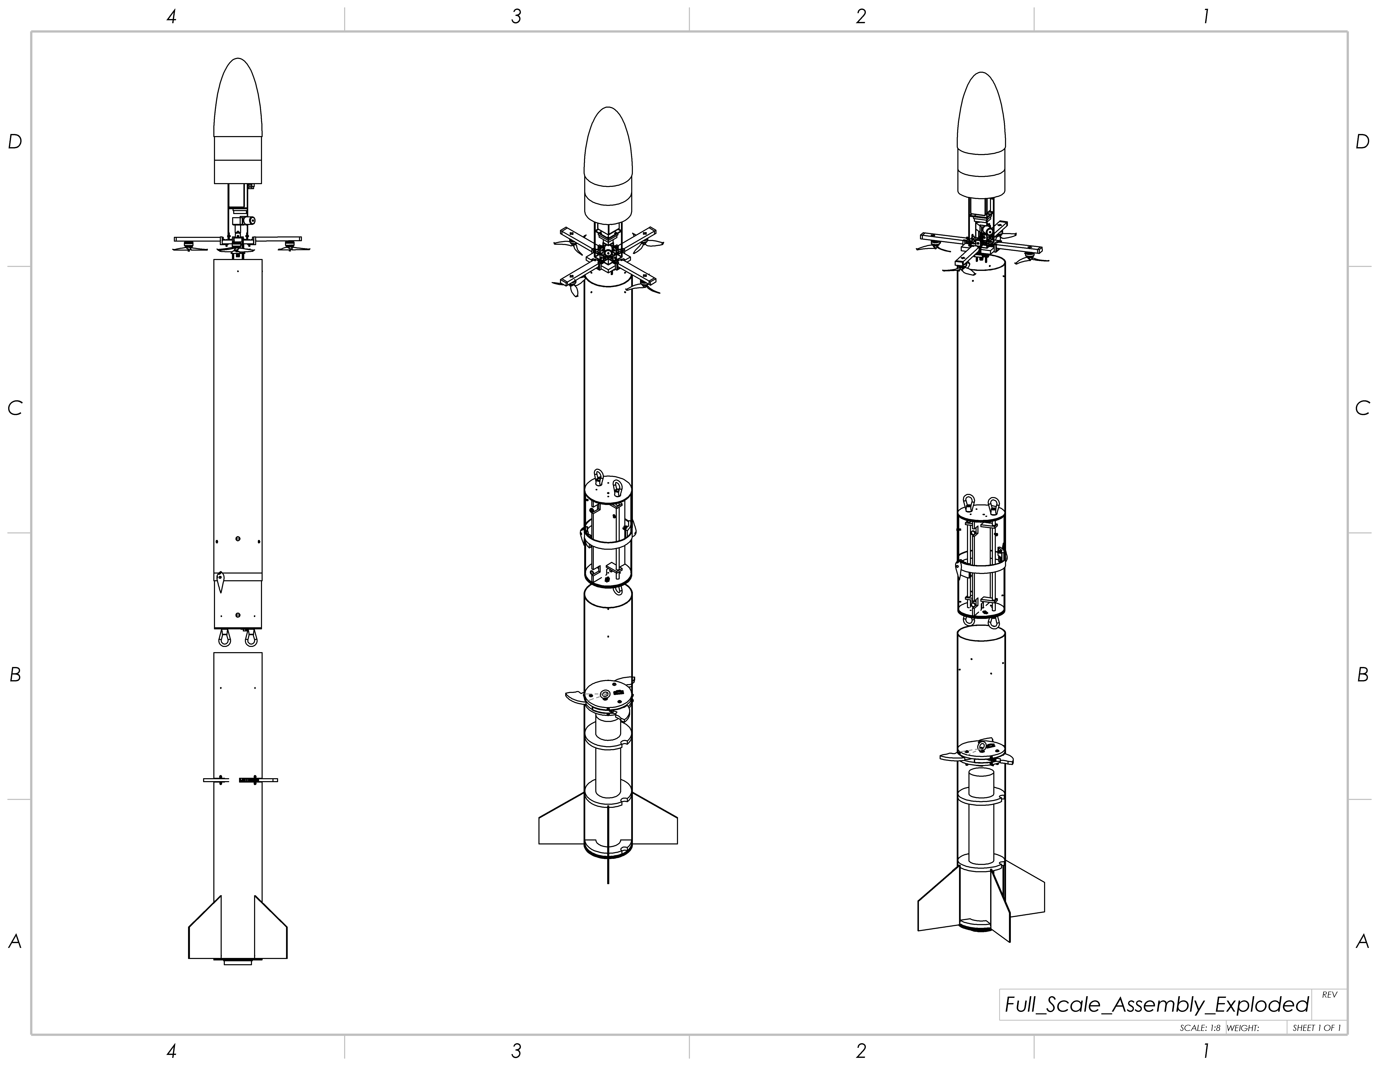
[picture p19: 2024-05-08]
Payload/Full Scale Rocket/Drawings/Images/Full_Scale_Assembly_Exploded.PNG

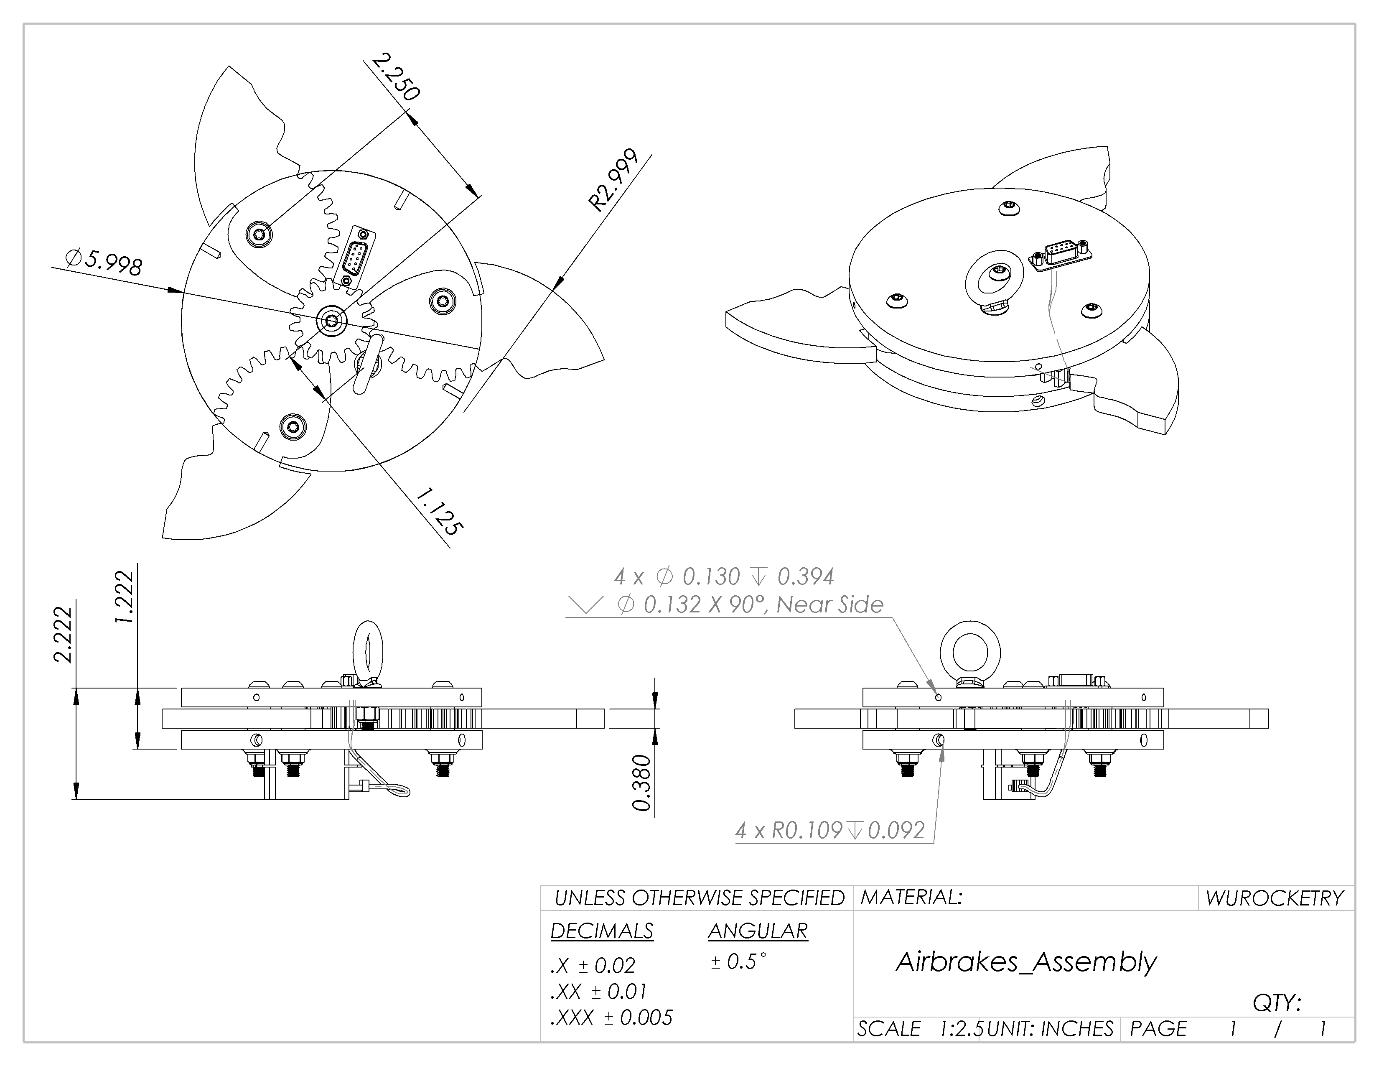
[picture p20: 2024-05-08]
Payload/Full Scale Rocket/Drawings/Images/Airbrakes_Assembly.PNG

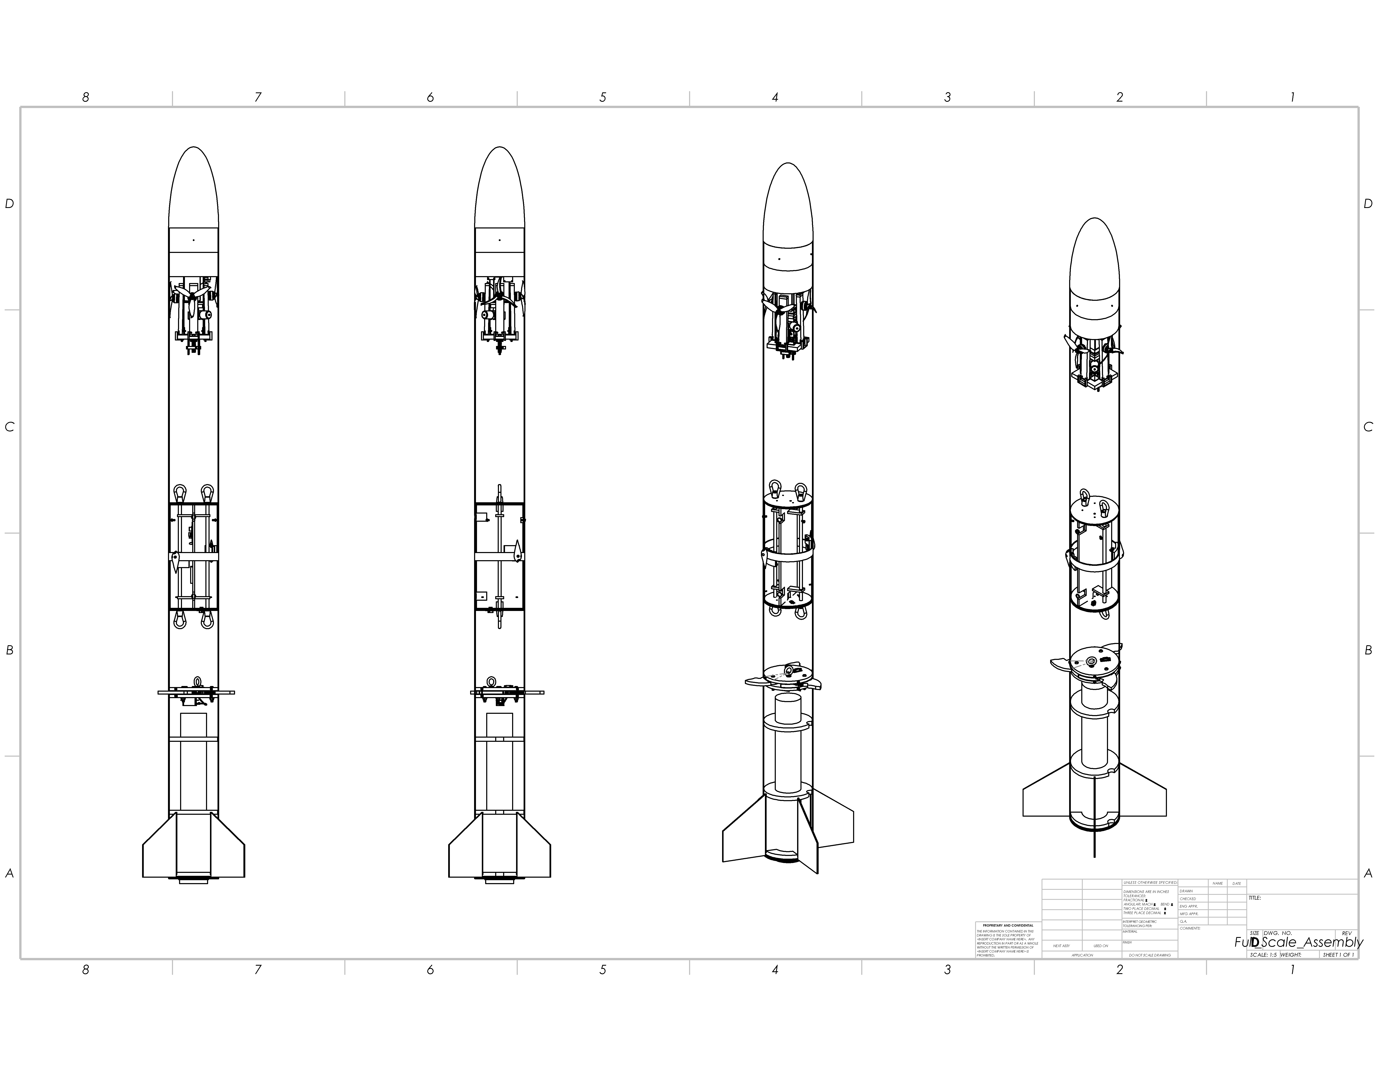
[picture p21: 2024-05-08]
Payload/Full Scale Rocket/Drawings/Images/Full_Scale_Assembly.PNG

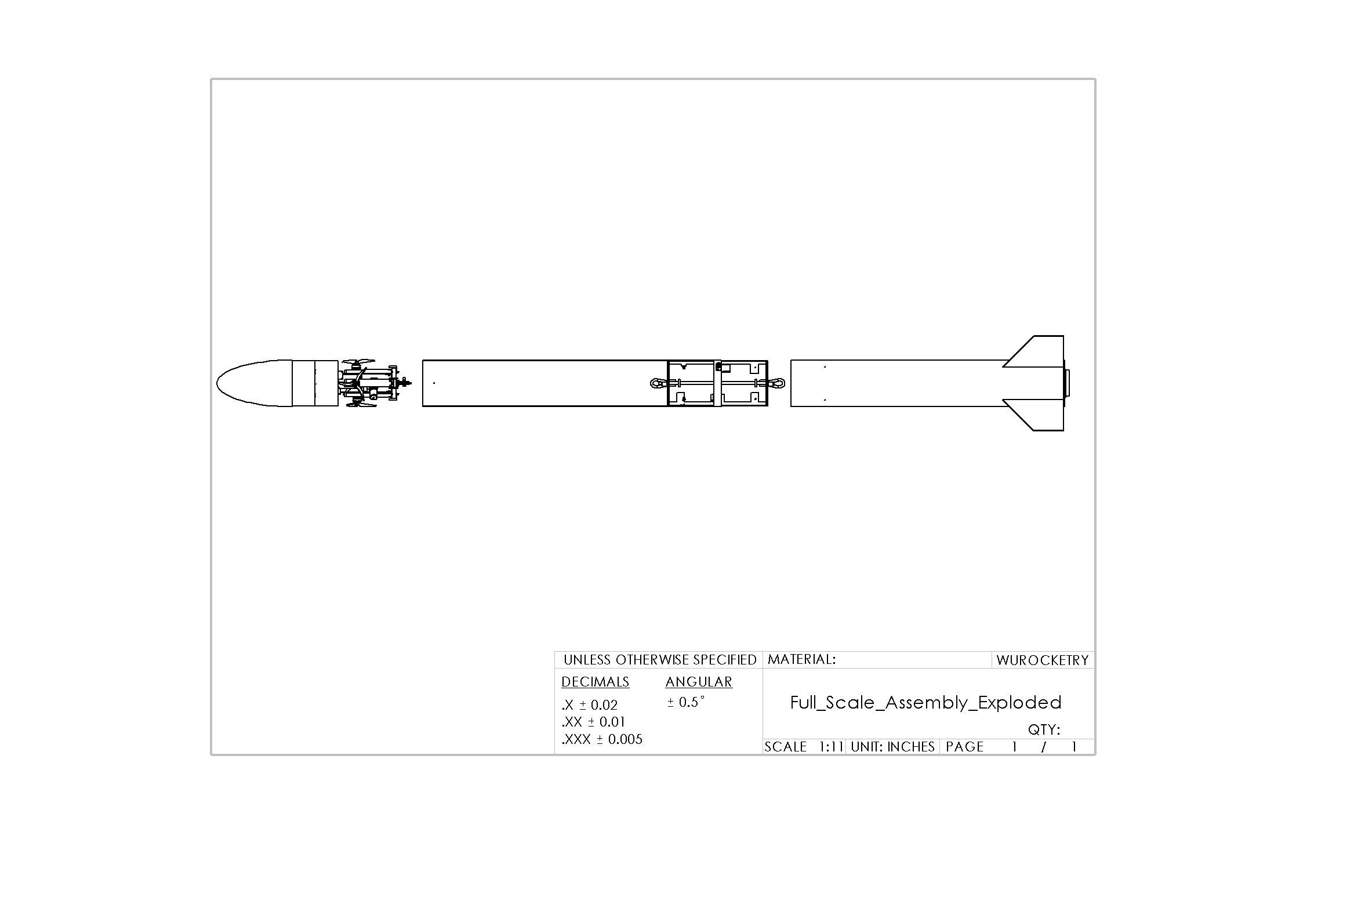
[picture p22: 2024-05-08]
Payload/Full Scale Rocket/Drawings/Overleaf/Full_Scale_Assembly_Exploded.JPG

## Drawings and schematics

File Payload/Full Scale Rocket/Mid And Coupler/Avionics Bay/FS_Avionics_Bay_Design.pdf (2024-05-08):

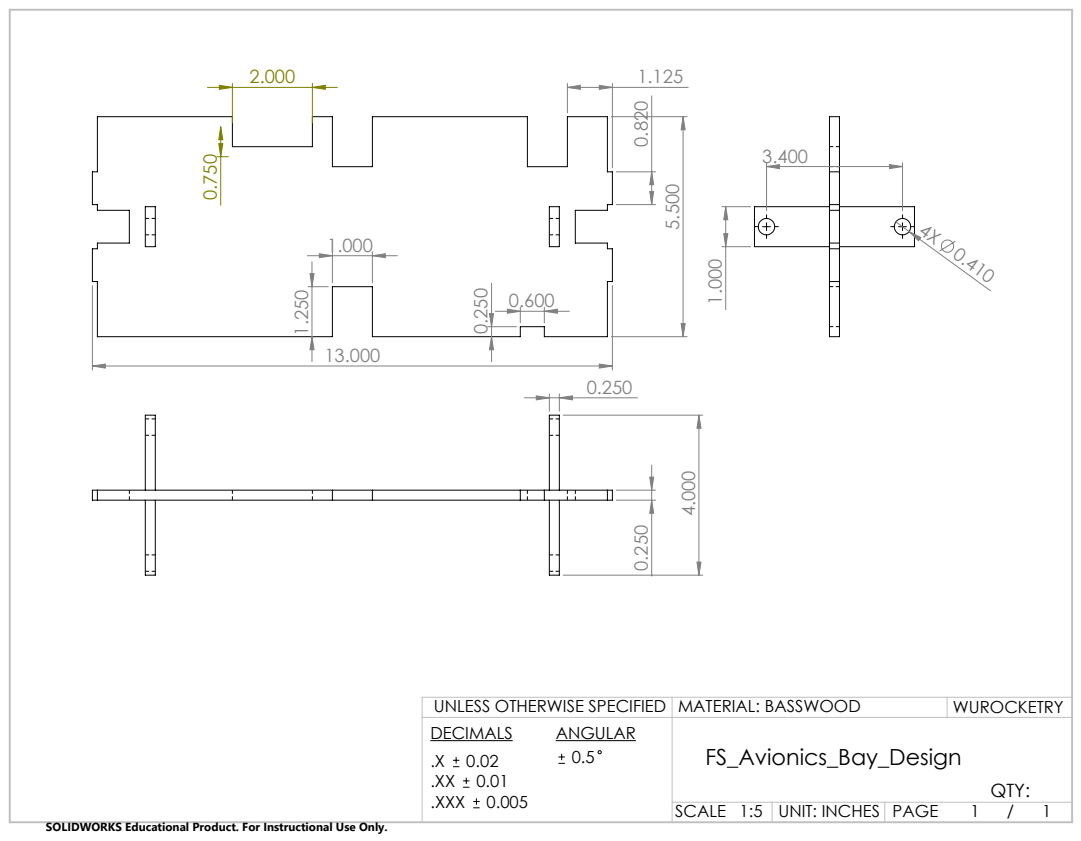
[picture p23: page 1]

UNLESS OTHERWISE SPECIFIED | MATERIAL: BASSWOOD | WUROCKETRY
DECIMALS | ANGULAR | | QTY:

SCALE 1:5 | UNIT: INCHES | PAGE 1 / 1

SOLIDWORKS Educational Product. For Instructional Use Only.

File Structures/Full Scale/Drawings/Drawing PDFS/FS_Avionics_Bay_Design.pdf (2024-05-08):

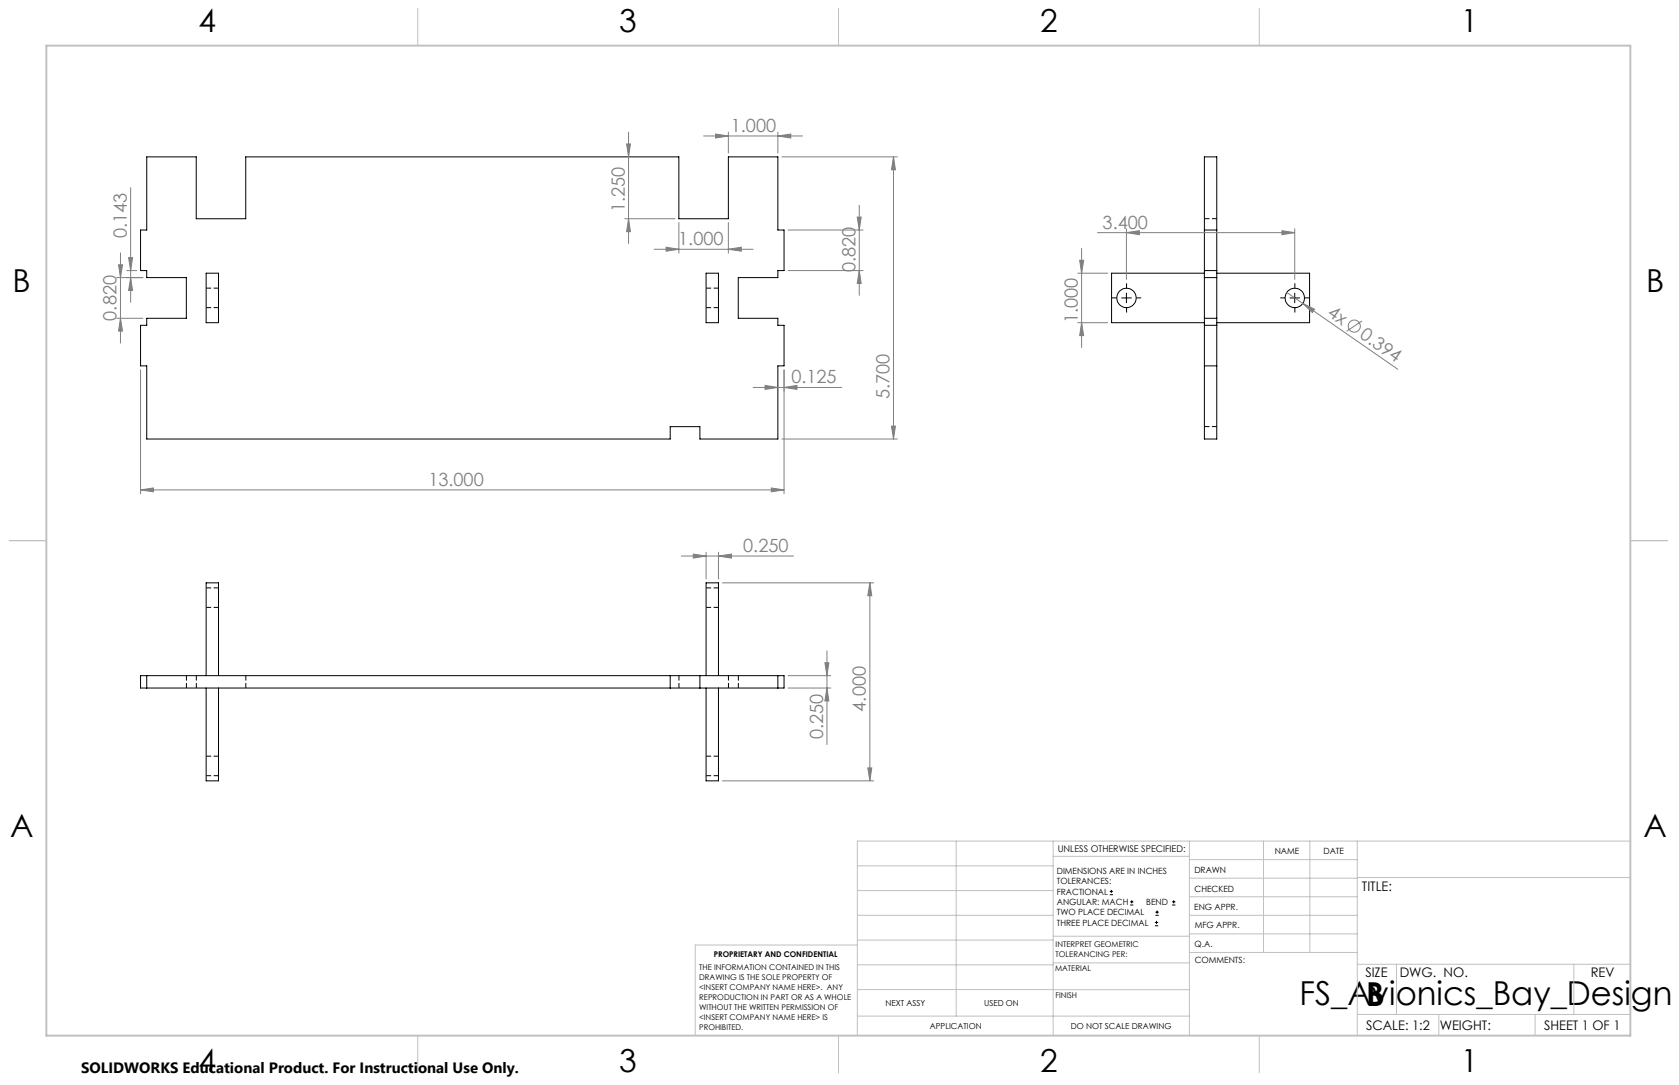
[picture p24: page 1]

UNLESS OTHERWISE SPECIFIED: | | NAME | DATE
DIMENSIONS ARE IN INCHES TOLERANCES: FRACTIONAL ANGULAR: MACH BEND TWO PLACE DECIMAL THREE PLACE DECIMAL | DRAWN

CHECKED | | | TITLE:

ENG APPR.
MFG APPR.

INTERPRET GEOMETRIC TOLERANCING PER: | Q.A.
MATERIAL | | SIZE B | DWG. NO. | REV

PROPRIETARY AND CONFIDENTIAL
THE INFORMATION CONTAINED IN THIS
DRAWING IS THE SOLE PROPERTY OF
<INSERT COMPANY NAME HERE>. ANY
REPRODUCTION IN PART OR AS A WHOLE
WITHOUT THE WRITTEN PERMISSION OF
<INSERT COMPANY NAME HERE> IS
PROHIBITED.

NEXT ASSY | USED ON | FINISH

APPLICATION | DO NOT SCALE DRAWING | | SCALE: 1:2 | WEIGHT: | SHEET 1 OF 1

SOLIDWORKS Educational Product. For Instructional Use Only.

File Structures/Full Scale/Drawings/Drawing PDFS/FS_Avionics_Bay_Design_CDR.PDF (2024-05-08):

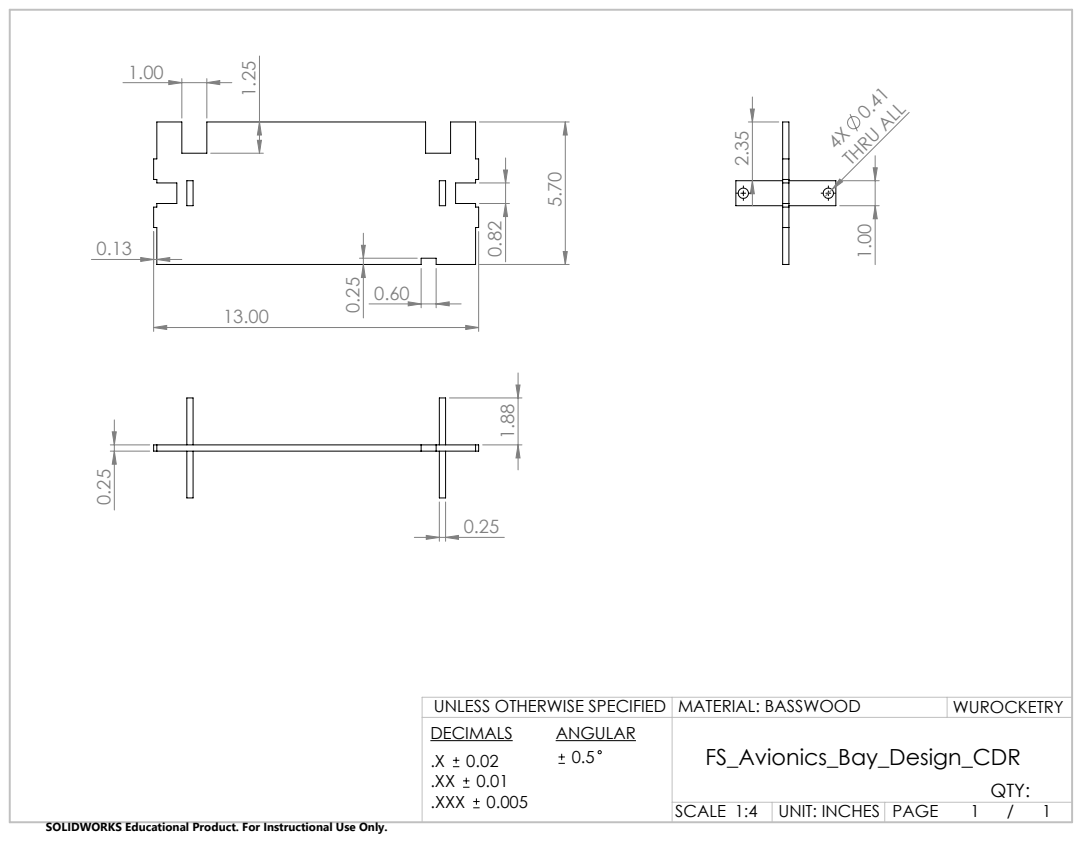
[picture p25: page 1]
THRU ALL

UNLESS OTHERWISE SPECIFIED | MATERIAL: BASSWOOD | WUROCKETRY
DECIMALS | ANGULAR | | QTY:

SCALE 1:4 | UNIT: INCHES | PAGE 1 / 1

SOLIDWORKS Educational Product. For Instructional Use Only.

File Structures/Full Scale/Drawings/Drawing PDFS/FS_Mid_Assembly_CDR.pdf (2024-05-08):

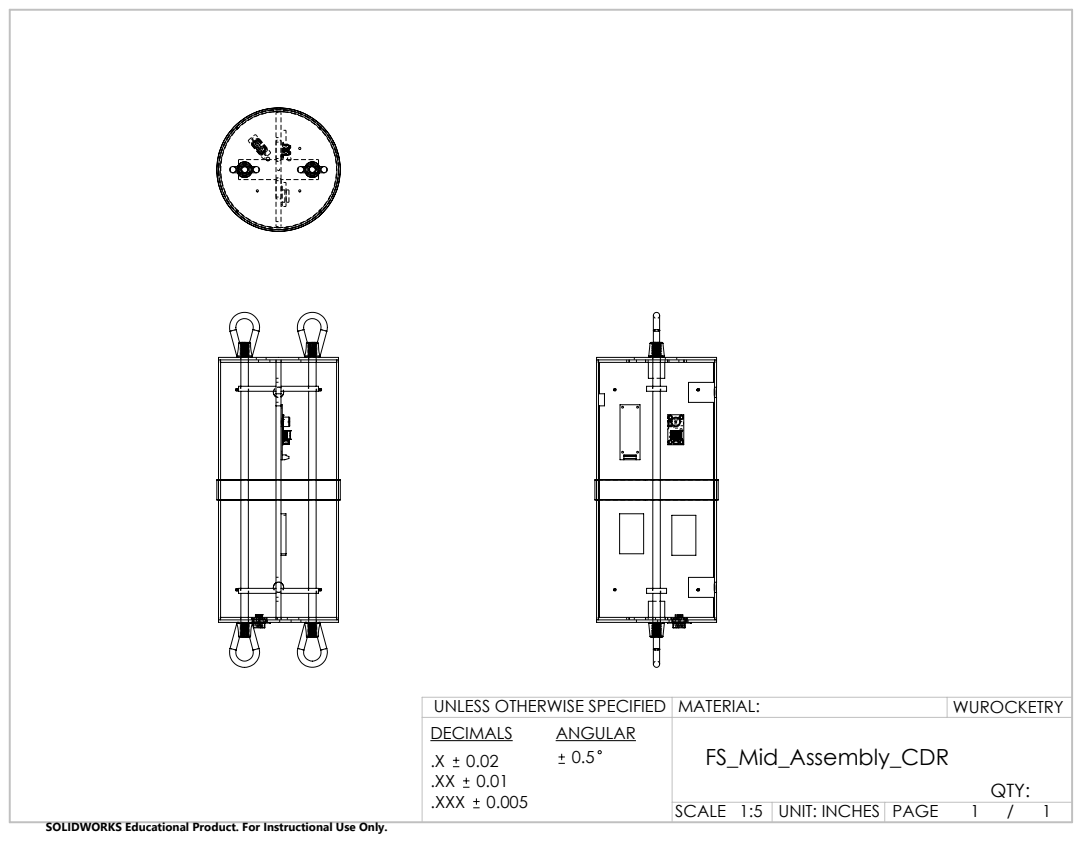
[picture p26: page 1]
UNLESS OTHERWISE SPECIFIED MATERIAL:; WUROCKETRY; FS_Mid_Assembly_CDR; .XX 0.01 .XXX 0.005; SCALE 1:5 UNIT: INCHES PAGE

SOLIDWORKS Educational Product. For Instructional Use Only.

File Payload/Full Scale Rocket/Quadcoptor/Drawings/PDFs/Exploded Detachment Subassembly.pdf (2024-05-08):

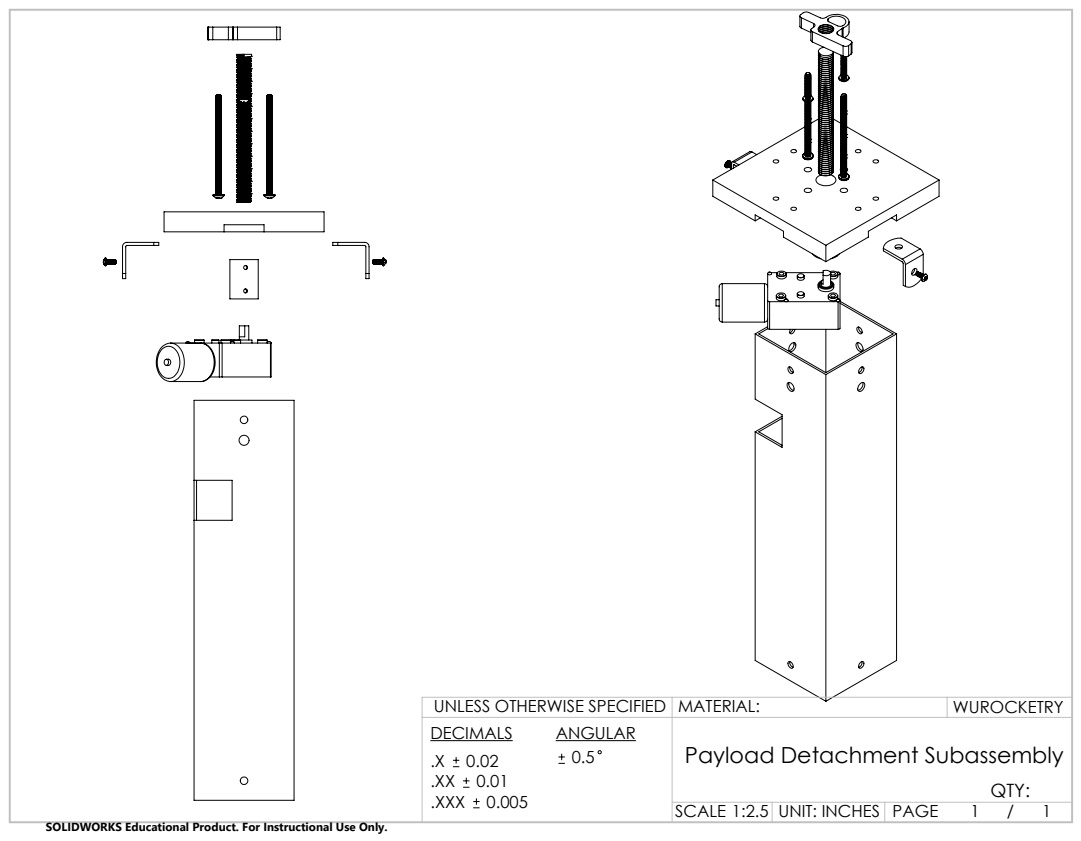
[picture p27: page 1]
Payload Detachment Subassembly

UNLESS OTHERWISE SPECIFIED | MATERIAL: | WUROCKETRY
DECIMALS | ANGULAR | | QTY:

SCALE 1:2.5 | UNIT: INCHES | PAGE 1 / 1

SOLIDWORKS Educational Product. For Instructional Use Only.

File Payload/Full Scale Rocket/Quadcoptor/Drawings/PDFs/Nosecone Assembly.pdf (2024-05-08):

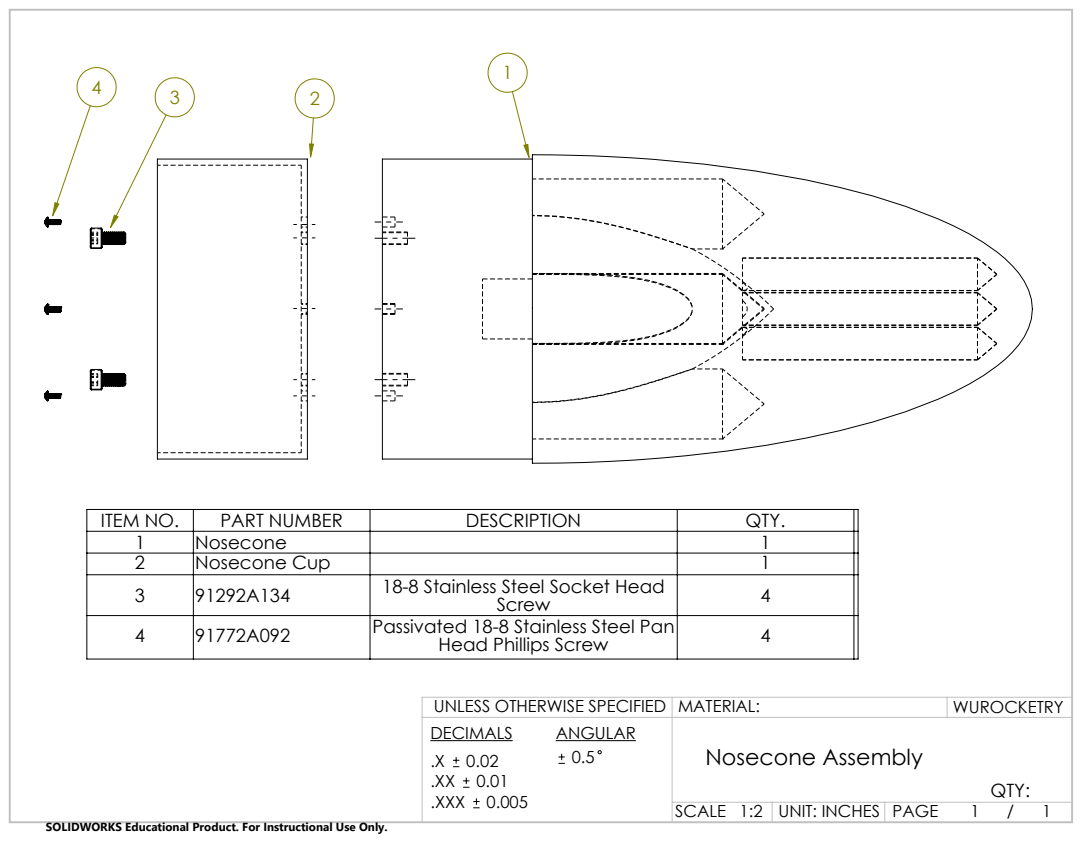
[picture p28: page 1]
Nosecone Assembly

ITEM NO. | PART NUMBER | DESCRIPTION | QTY.
1 | Nosecone | | 1
2 | Nosecone Cup | | 1
3 | 91292A134 | 18-8 Stainless Steel Socket Head Screw | 4
4 | 91772A092 | Passivated 18-8 Stainless Steel Pan Head Phillips Screw | 4

UNLESS OTHERWISE SPECIFIED | MATERIAL: | WUROCKETRY
DECIMALS | ANGULAR | | QTY:

SCALE 1:2 | UNIT: INCHES | PAGE 1 / 1

SOLIDWORKS Educational Product. For Instructional Use Only.

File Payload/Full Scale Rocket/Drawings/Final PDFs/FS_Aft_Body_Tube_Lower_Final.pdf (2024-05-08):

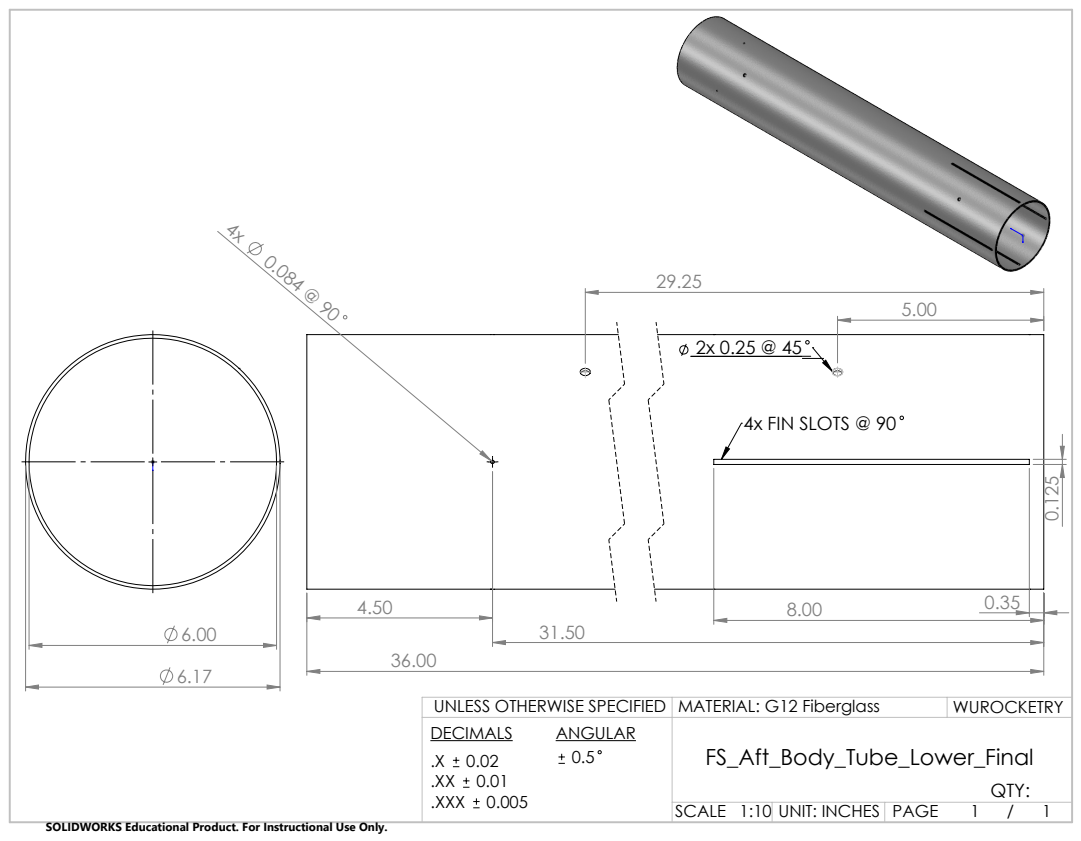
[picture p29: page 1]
4x FIN SLOTS @ 90

UNLESS OTHERWISE SPECIFIED | MATERIAL: G12 Fiberglass | WUROCKETRY
DECIMALS | ANGULAR | | QTY:

SCALE 1:10 UNIT: INCHES | | PAGE 1 / 1

SOLIDWORKS Educational Product. For Instructional Use Only.

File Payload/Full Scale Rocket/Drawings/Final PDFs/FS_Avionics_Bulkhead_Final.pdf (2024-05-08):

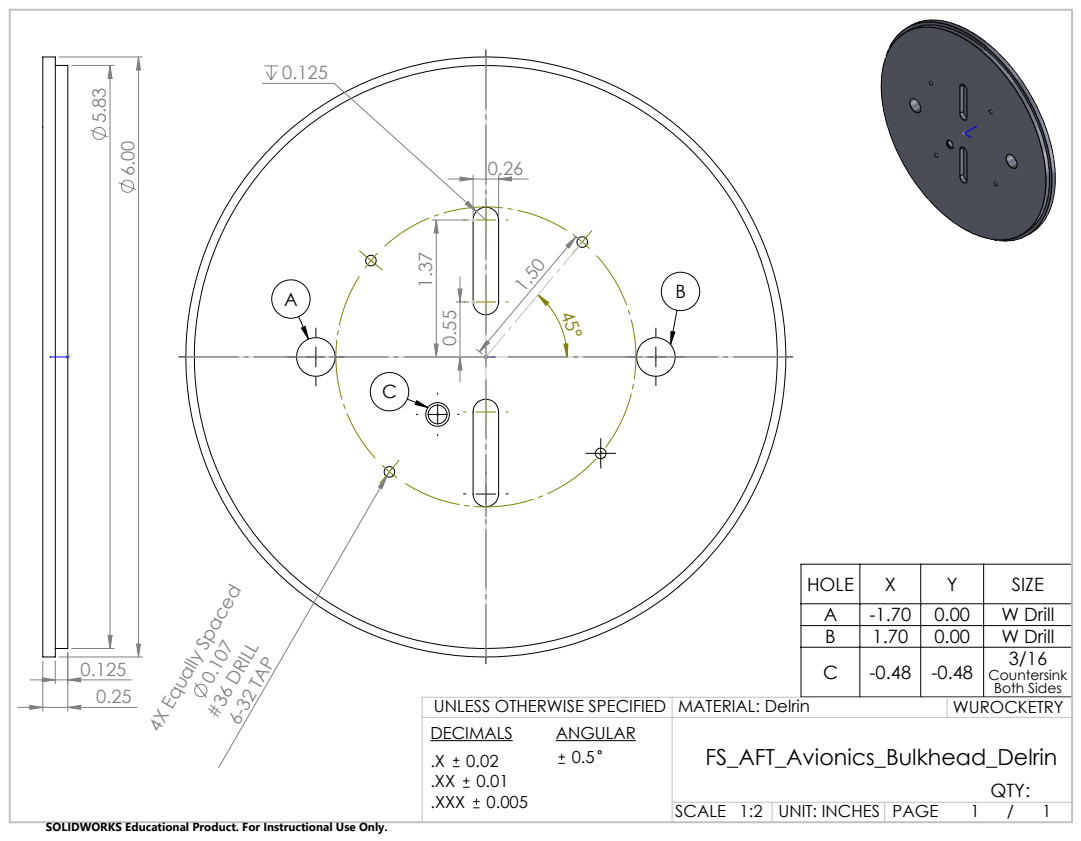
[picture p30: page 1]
4X Equally Spaced; #36 DRILL 6-32 TAP

HOLE | X | Y | SIZE
A | -1.70 | 0.00 | W Drill
B | 1.70 | 0.00 | W Drill
C | -0.48 | -0.48 | 3/16 Countersink Both Sides

UNLESS OTHERWISE SPECIFIED | MATERIAL: Delrin | WUROCKETRY
DECIMALS | ANGULAR | | QTY:

SCALE 1:2 | UNIT: INCHES | PAGE 1 / 1

SOLIDWORKS Educational Product. For Instructional Use Only.

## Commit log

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2023-06-30 Add files via upload
    Full-scale Forward Bulkhead V2 (added airframe mounting holes)
    [FS FWD Bulkhead.SLDPRT]
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2023-07-06 Add files via upload
    Forward Bulkhead Version 3 (updated 6-32 airframe mounting screw hole depths)
    Forward Avionics Bulkhead (first commit)
    Aft Avionics Bulkhead (first commit)
    [FS AFT Avionics Bulkhead.SLDPRT, FS FWD Avionics Bulkhead.SLDPRT, FS FWD Bulkhead.SLDPRT]
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2023-07-06 Add files via upload
    FS Forward, Forward Avionics, and Aft Avionics Bulkheads. Uploaded to the dev/structures branch instead of just the structures folder (hey I'm bad at GitHub don't judge (o ) (o ))
    [FS AFT Avionics Bulkhead.SLDPRT, FS FWD Avionics Bulkhead.SLDPRT, FS FWD Bulkhead.SLDPRT]
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2023-07-08 Add files via upload
    Adding Subscale Avionics Bulkheads. For the Avionics Board dimensions, I didn't change hole or slot spacing, so it SHOULD be alright. If it's not, it wouldn't be the first time.
    [SS AFT Avionics Bulkhead.SLDPRT, SS FWD Avionics Bulkhead.SLDPRT]
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2023-07-10 Airbrakes Overhaul
    Updated Aft Assembly with airbrakes paddles, gears, and stand-in servo. Added in Additional bulkhead for the motor section. We need to think about the weight of the rocket now. All of these parts wil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
    [FS_Aft_Assembly.SLDASM, FS_Aft_Body_Tube_Lower.SLDPRT, FS_Aft_Body_Tube_Upper.SLDPRT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]
2023-07-10 Fix Motor part
    [FS_Aft_Assembly.SLDASM, FS_Airbrake_Forward_Bukhead.SLDPRT, FS_Airbrake_Paddle.SLDPRT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]
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2023-07-13 Cam Holders (working)
    Working cam holders for now, needs to be updated later on
    [FS_camholders.SLDPRT]
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2023-07-23 Remove references to old assembly + update airbrake (needs to be revised)
    [FS_Airbrake_Assembly.SLDASM, FS_Airbrake_Paddle.SLDPRT, FS_Airbrakes_Section_Coupler.SLDPRT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]
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2023-07-26 Slightly improve Fins
    I really dislike what I have done. Would be great if this were more elegant.
    [FS_Airbrake_Paddle.SLDPRT]
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2023-08-04 Forward Avionics and Aft Avionics Bulkheads adjustment for design overhaul
    Decreased thickness to 0.25 from 0.375, eliminated central eye bolt hole
    [FS AFT Avionics Bulkhead.SLDPRT, FS FWD Avionics Bulkhead.SLDPRT]
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2023-08-14 Major Airbrakes overhall
    Fixed coupler rebuild errors, fixed resulting assembly errors, and fixed fins.
    TODO:
    compress length
    add thrust bearings as spacers
    make the airbrakes shape more simple
    create space for wire pass throughs
    add DB9 port
    [FS_Airbrake_Assembly.SLDASM, FS_Airbrake_Drive_Gear.sldprt, FS_Airbrake_Paddle.SLDPRT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]
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2023-08-23 Preliminary Glider Design CAD
    CAD for preliminary glider, front is a bit whack and off sized but the rest isnt so bad
    [PreliminaryPayloadGlider01.SLDPRT]
2023-08-23 Glider Preliminary CAD
    Front is whack but the rest isnt so bad, it gets the idea across
    [PreliminaryPayloadGlider01.SLDPRT]
2023-08-23 Delete PreliminaryPayloadGlider01.SLDPRT
    This was initially placed in the wrong spot which is why I am deleting it
    [PreliminaryPayloadGlider01.SLDPRT]
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2023-09-04 Metric Revamp and Mounting Bracket Redesign
    Also made a folder for manufacturing jigs. Adjusted forward bulkhead for metric screws and for use with its manufacturing jig.
    On the Airbrakes, I increased the thickness of the paddles, replaced the mounting bracket with its new version for 3D printing, and replaced hardware with metric equivalents (and sized relevant holes in parts accordingly).
    [3014T45_Steel Eyebolt with Shoulder - for Lifting.SLDPRT, 4843T11_Galvanized Steel Eyebolt - for Lifting.SLDPRT, 90630A110_High-Strength Steel Nylon-Insert Loc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]
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2023-09-05 Fix Eyebolt in FWD assembly
    [FS AFT Avionics Bulkhead.SLDPRT, FS FWD Avionics Bulkhead.SLDPRT, FS_Aft_Body_Tube_Lower.SLDPRT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]
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2023-09-06 Revert "Update Random Files"
    This reverts commit c73ca4172907818c3e59b0683f7da350f2384ce5.
    [FS_Airbrake_Paddle.SLDPRT, FS_Airbrakes_Section_Coupler.SLDPRT, FS_Center_Bushing.SLDPRT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]
2023-09-06 Mechanical update
    I pulled, stashed, and now I'm committing my changes. Hopefully this works as intended.
    [5906K531_Oil-Embedded Thrust Bronze Bearing.SLDPRT, 7811K128_Multipurpose 660 Leaded Sleeve Bearing.SLDPRT, 90910A587_Button Head Torx Screws.SLDPRT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]
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2023-09-07 SS CAD Updates to Metric
    Only FWD and Aft. Also manufacturing jigs for fwd and aft bulkheads. And dimensional drawing for SS Aft Bulkhead.
    [SS_Aft_Bulkhead.SLDDRW, SS_Aft_Bulkhead.SLDPRT, SS_Aft_Bulkhead_Jig_p1.SLDPRT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]
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2023-09-18 Shrink FS Aft Assembly to SS Aft Assembly
    Screw holes needs to be figured out for airbrakes bulkhead
    [4843T11_Galvanized Steel Eyebolt - for Lifting.SLDPRT, 7811K128_Multipurpose 660 Leaded Sleeve Bearing.SLDPRT, 90910A587_Button Head Torx Screws.SLDPRT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]
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2023-09-19 Manufacturing Updates
    William completely remade my SS aft bulkhead instead of modifying it so my drawing would still function :'(
    [FS_Airbrakes_Section_Coupler.SLDPRT, SS AFT Avionics Bulkhead.SLDPRT, SS_Aft_Avionics_Bulkhead.SLDDRW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]
2023-09-20 Bulkhead hole change: Lead screw diameter change
    Also made me update the SS assembly file and its dependents to the newest version since I had it open and it didn't like me closing it. The files I actually changed were the forward avionics and aft avionics bulkheads and their respective drawings.
    [3274T41_Steel Oval Eye Nut- for Lifting.SLDPRT, 4843T11_Galvanized Steel Eyebolt - for Lifting.SLDPRT, 7811K128_Multipurpose 660 Leaded Sleeve Bearing.SLDPRT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]
2023-09-20 Bulkhead Drawings Update
    Fixed a hole callout in Aft Bulkhead and updated the pdf versions of the avionics bulkhead drawings to the current version
    [FS_Airbrakes_Section_Coupler.SLDPRT]
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2023-09-21 Minor Touch-ups
    Replace FS motor hardware with SS hardware, improve paddles, add back SS bulkhead
    [FS_L1520_Blue_Thunder.SLDPRT, SS AFT Avionics Bulkhead.SLDPRT, SS FWD Avionics Bulkhead.SLDPRT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]
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2023-09-24 SS ASM Screws
    Added M4 screws to subscale assembly and fixed diameter of forward bulkhead
    [90991A122_18-8 Stainless Steel Button Head Torx Screws.SLDPRT, FS_L1520_Blue_Thunder.SLDPRT, SS AFT Avionics Bulkhead.SLDPRT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]
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2023-09-28 Fixture and Camera Bracket Upload
    [SS_Camera_Bracket.SLDPRT, Test_Fixture.SLDPRT]
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2023-10-03 3D printed file for Airbrakes slot fixture
    [Airbrakes_Slot_Fixture.STL]
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2023-10-04 Added shear screw holes to ss aft body tube
    2" from forward edge of the body tube
    0.086" Diameter (#44 Drill Bit)
    [SS_Aft_Body_Tube_Lower.SLDPRT]
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2023-10-04 Drawing for Avionics Coupler Hole
    Super duper basic drawing of hole location
    [SS_Aft_Body_Tube_Lower_Avionics_Hole.SLDDRW]
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2023-10-05 AB Mounting bracket heat insert hole size, aft body tube shear screw hole location, AB mounting holes on aft body tube
    [SS_Aft_Body_Tube_Lower.SLDDRW, SS_Aft_Body_Tube_Lower.SLDPRT, SS_Mounting_Bracket.SLDPRT]
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2023-10-11 Coupler drawing pdf
    I'm not uploading the actual drawing because I changed the model to make the drawing easier and I don't want my change to break anything in the assembly. It was just flipping where holes were cut so that the drawing was easier to make. Nothing important.
2023-10-11 Aft Bulkhead Jig Fixed
    [Aft Bulkhead Jig Visualization.SLDASM, SS_Aft_Bulkhead_Jig_p1.SLDPRT, SS_Aft_Bulkhead_Jig_p1.STL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]
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2023-10-11 Correct Length of Nosecone
    [SS_Elliptical_Nosecone_combined.SLDPRT]
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2023-10-15 Bulkhead PDR Writing CAD Updates
    Updated FS Fwd bulkhead to match SS, added terminal block holes to SS FWD and AFT Avionics Bulkheads, and updated the SS FWD Assembly
    [4843T11_Galvanized Steel Eyebolt - for Lifting.SLDPRT, 92673A113_18-8 Stainless Steel Hex Nut.SLDPRT, FS FWD Bulkhead.SLDPRT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]
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2023-10-22 Update SS_Elliptical_Nosecone_combined.SLDPRT
    Deeper and larger eye bolt hole, chamfer on heat set insert holes. Still does not need supports to print
    [SS_Elliptical_Nosecone_combined.SLDPRT]
2023-10-23 Airbrakes Drive Gear Edit
    Preliminary design for new airbrakes drive gear that will connect to the servo gear.
    [SS_Airbrake_Drive_Gear.SLDPRT, SS_Mounting_Bracket.SLDPRT, SavoxServo.SLDPRT]
2023-10-25 Update Drive Gear
    Added cut for servo gear in airbrakes drive gear
    [Harness_5-FS_Airbrake_Assembly.SLDASM, SS_Airbrake_Drive_Gear.SLDPRT]
2023-10-25 Misc updates
    Airbrake mounting bracket heat set insert holes are slightly larger and I added a chamfer (requested by Theo on the nosecone) for easier installation.
    Also deleted a ghost hole on the nosecone
    [SS_Elliptical_Nosecone_combined.SLDPRT, SS_Mounting_Bracket.SLDPRT]
2023-10-25 AB Drive Gear Alternate Part
    Alternate part to try printing in addition to the non-toleranced part. This part matches the tolerancing fit profile on the paddle gears. Visually, it is distinguishable by a small, thin slot cut into its base
    [SS_Airbrake_Drive_Gear_02_Smaller.SLDPRT, SS_Airbrake_Drive_Gear_03_smaller.SLDPRT, SS_Airbrake_Drive_Gear_05_smaller.SLDPRT]
2023-10-25 Create SS_Airbrake_Paddle_edited_02_smaller.SLDPRT
    Added over-extension stop for when people are playing with it it won't go past the last tooth
    Added a fillet to the tip so it won't get snagged on the body tube as easily
    Increased the center hole diameter for a free fit instead of a press fit
    Increased body tube clearance slot slightly
    Added engraved aft side label to help with assembly
    Removed teeth that aren't used
    [SS_Airbrake_Paddle_edited_02_smaller.SLDPRT]
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2023-10-29 Fullscale Fin Drawing
    Made folders for Solidworks Drawings and PDF versions of them
    [FS_Basic_Fin.SLDDRW]
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2023-10-31 Corrected length of avionics board
    [FS_Avionics_Bay_Design.SLDPRT]
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2023-11-04 Subscale CAD Update
    Avionics Bay Cut for 3D updated, added in the missing leadscrew from the mid coupler assembly
    [FS_L1520_Blue_Thunder.SLDPRT, SS AFT Avionics Bulkhead.SLDPRT, SS FWD Avionics Bulkhead.SLDPRT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]
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2023-11-05 fix lead_screw_diam equation from 11mm to .386in
    [FS FWD Avionics Bulkhead.SLDPRT]
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2023-11-09 Fixed the mate issues with the aft assembly
    [AvionicsBoard.SLDASM, FS AFT Avionics Bulkhead.SLDPRT, FS FWD Avionics Bulkhead.SLDPRT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]
2023-11-09 aft assembly fixed
2023-11-09 full scale CAD fixed
    [FS AFT Avionics Bulkhead.SLDPRT, FS FWD Avionics Bulkhead.SLDPRT, FS_Aft_Body_Tube_Lower.SLDPRT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]
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2023-12-08 added clearance to fin jig
    [FS_Coupler_Fixture.SLDPRT, FS_Coupler_Fixture.STL]
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2023-12-28 Sub Scale Drawings
    Drawing itself is excluded because it is too big
    [FS_L1520_Blue_Thunder.SLDPRT, SS AFT Avionics Bulkhead.SLDPRT, SS FWD Avionics Bulkhead.SLDPRT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]
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2023-12-29 Fix Airbrakes Screws
    [FS_Aft_Body_Tube_Lower.SLDPRT, FS_Airbrake_Paddle.SLDPRT, FS_Airbrakes_Section_Coupler.SLDPRT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]
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2024-01-22 AB Redesign
    Mostly SS but some FS. Moved FS mounting holes and am working on everything SS. Not finished yet.
    [FS_Aft_Body_Tube_Lower.SLDPRT, SS_Aft_Body_Tube_Lower.SLDPRT, SS_Airbrake_Drive_Gear.SLDPRT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]
2024-01-22 AB redesign
    SS finished AB redesign
    [7811K129_Multipurpose 660 Leaded Sleeve Bearing.SLDPRT, 92832A591_Zinc-Plated Alloy Steel Button Head Torx Screws.SLDPRT, Harness_5-FS_Airbrake_Assembly.SLDASM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]
2024-01-22 SS AB redesign
    Finished SS AB redesign. Still need to do FS
    [7811K122_Multipurpose 660 Leaded Sleeve Bearing.SLDPRT, 92832A590_Zinc-Plated Alloy Steel Button Head Torx Screws.SLDPRT, FS_L1520_Blue_Thunder.SLDPRT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]
2024-01-22 Fix FS AB mounting holes to match SS update redesign
    still working on AB redesign, but William mentioned working on the FS body tube tonight, so I wanted to make sure this is updated
    [FS_Aft_Body_Tube_Lower.SLDPRT]
2024-01-22 FS Airbrake Redesign
    Mostly finished. Made paddle gear adjustments on the main file. The central drive gear as not had the clearance edits we made on the subscale printed files yet.
    [7811K128_Multipurpose 660 Leaded Sleeve Bearing.SLDPRT, 7811K129_Multipurpose 660 Leaded Sleeve Bearing.SLDPRT, 92832A590_Zinc-Plated Alloy Steel Button Head T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]
2024-01-28 FS AB Mounting Support Redesign
    Beefier screw mounts, deeper heat set insert holes, embedded nut retainers. Still need to re-slice at selective higher infill and move the eye bolt to the center of the bulkhead
    [FS_Airbrake_Drive_Gear.sldprt, FS_Center_Bushing.SLDPRT, FS_Mounting_Bracket.SLDPRT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]
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2024-02-04 Airbrakes Slots
    Fixed airbrake slot geometry to reflect machining
    [FS_Aft_Body_Tube_Lower.SLDPRT]
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2024-02-24 Add rotated bulkhead file
    This was only for machining purposes. We needed the origin rotated for machining and I didn't want to break anything in any assembly
    [FS_Aft_Bulkhead_rotated.SLDPRT]
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2024-02-28 Mid/Coupler assy fix, add second rail button to aft tube, remove db9 from aft avionics bulkhead
    [FS FWD Avionics Bulkhead.SLDPRT, FS_AFT_Avionics_Bulkhead_Delrin.SLDPRT, FS_Aft_Body_Tube_Lower.SLDDRW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]
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2024-02-28 Correct m4 connection holes between mid and aft
    [FS_Avionics_Coupler.SLDPRT, FS_Camera_Bracket.SLDPRT, FS_Lead_Screw.SLDPRT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]
2024-02-28 Fix a few rebuild errors
    [FS_AFT_Avionics_Bulkhead_Delrin.SLDPRT, FS_Aft_Assembly.SLDASM, FS_Aft_Body_Tube_Lower.SLDPRT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]
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2024-02-29 Fix assembly
    [FS AFT Avionics Bulkhead.SLDPRT, FS FWD Avionics Bulkhead.SLDPRT, FS_Aft_Assembly.SLDASM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]
2024-03-02 Replace bulkheads with delrin bulkhead
    [FS FWD Avionics Bulkhead.SLDPRT, FS_Avionics_Bulkhead_Final.SLDPRT, FS_Avionics_Coupler.SLDPRT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]
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
